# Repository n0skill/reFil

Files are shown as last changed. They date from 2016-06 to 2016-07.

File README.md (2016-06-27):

# reFil
A machine that makes filament suitable for 3D printers out of normally unrecycled plastic parts such as HDPE from bottle caps, failed prints etc.

# Folders
* schematics - All of the schematics made with KiCAD. Including the gerber files, kicad files (schematic, netlist, pcb, etc.)
* src - The source code running on the arduino nano (arduino/C/AVR ASM)
* mechanics - mechanical parts

# Material
The following material is needed for the whole project.

## Mechanical parts
The machine is made of lathed aluminium and brass.
All the plans will be available in the "mechanical" folder. Including 3D models, plans and specs

## Electrical parts
The controller board consists of an arduino nano and a custom board. Using a 24V power supply, a LM7805 regulator is used to drop down the voltage to a usable 5V signal to drive the logic. Since the drop is quite significant and the LM7805 is a simple linear regulator, a decent amount of heat will be produced. This can compromise the functionality of the circuit, so a heat sink has to be appended to it in order to better disipate the heat.

The board will be used to: 
1) display the current temperature
2) drive the motor
3) drive the heating element

### Temperature sensor
The temperature sensor consists of a PT1000 RTD as part of a voltage divider circuit. The conversion from voltage to temperature can be made by either: looking up a table, or using a formula.

Once the temperature is known, the arduino uses BCD encoding to controll the CD4543BE 7 segment display driver, which displays the temperature.

### Motor driver
The motor is a E192.24.246 Micromotors brushed DC thing. It has a 1:246 gearbox that allows it to move things with a high torque (at the expense of a lower rate of rotation. But we don't care about that)

It is using the 24V from the barrel jack and is toggled using a SRD-05VDC-SL-C relay from SONGLE industries.

### Heating element

The heating element is a simple nichrome wire that is also toggled with a relay on the 24V power line.

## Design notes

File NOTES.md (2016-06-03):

# Todo

## Currently
* Add temperature display
* Develop board to sense heat, control nichrome wire alimentation§ 

## Future Releases
* Add multiple thermal sensors to homogenize temp in core
* Add multiple thermal resistances to homogenize temp

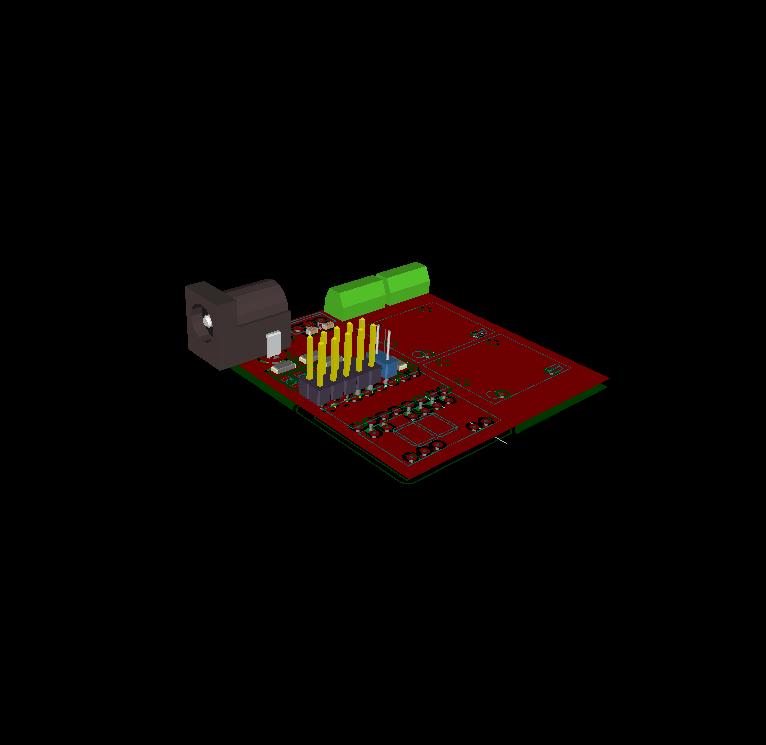
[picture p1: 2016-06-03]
schematics/reFil.jpg

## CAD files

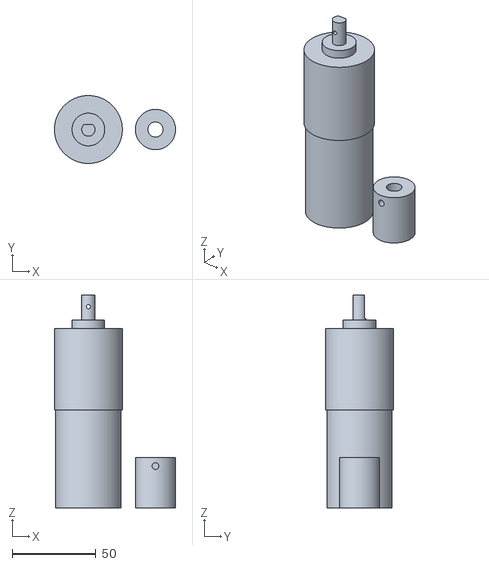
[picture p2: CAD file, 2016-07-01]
mechanic/parts.stl
72.2 x 40.5 x 127.0

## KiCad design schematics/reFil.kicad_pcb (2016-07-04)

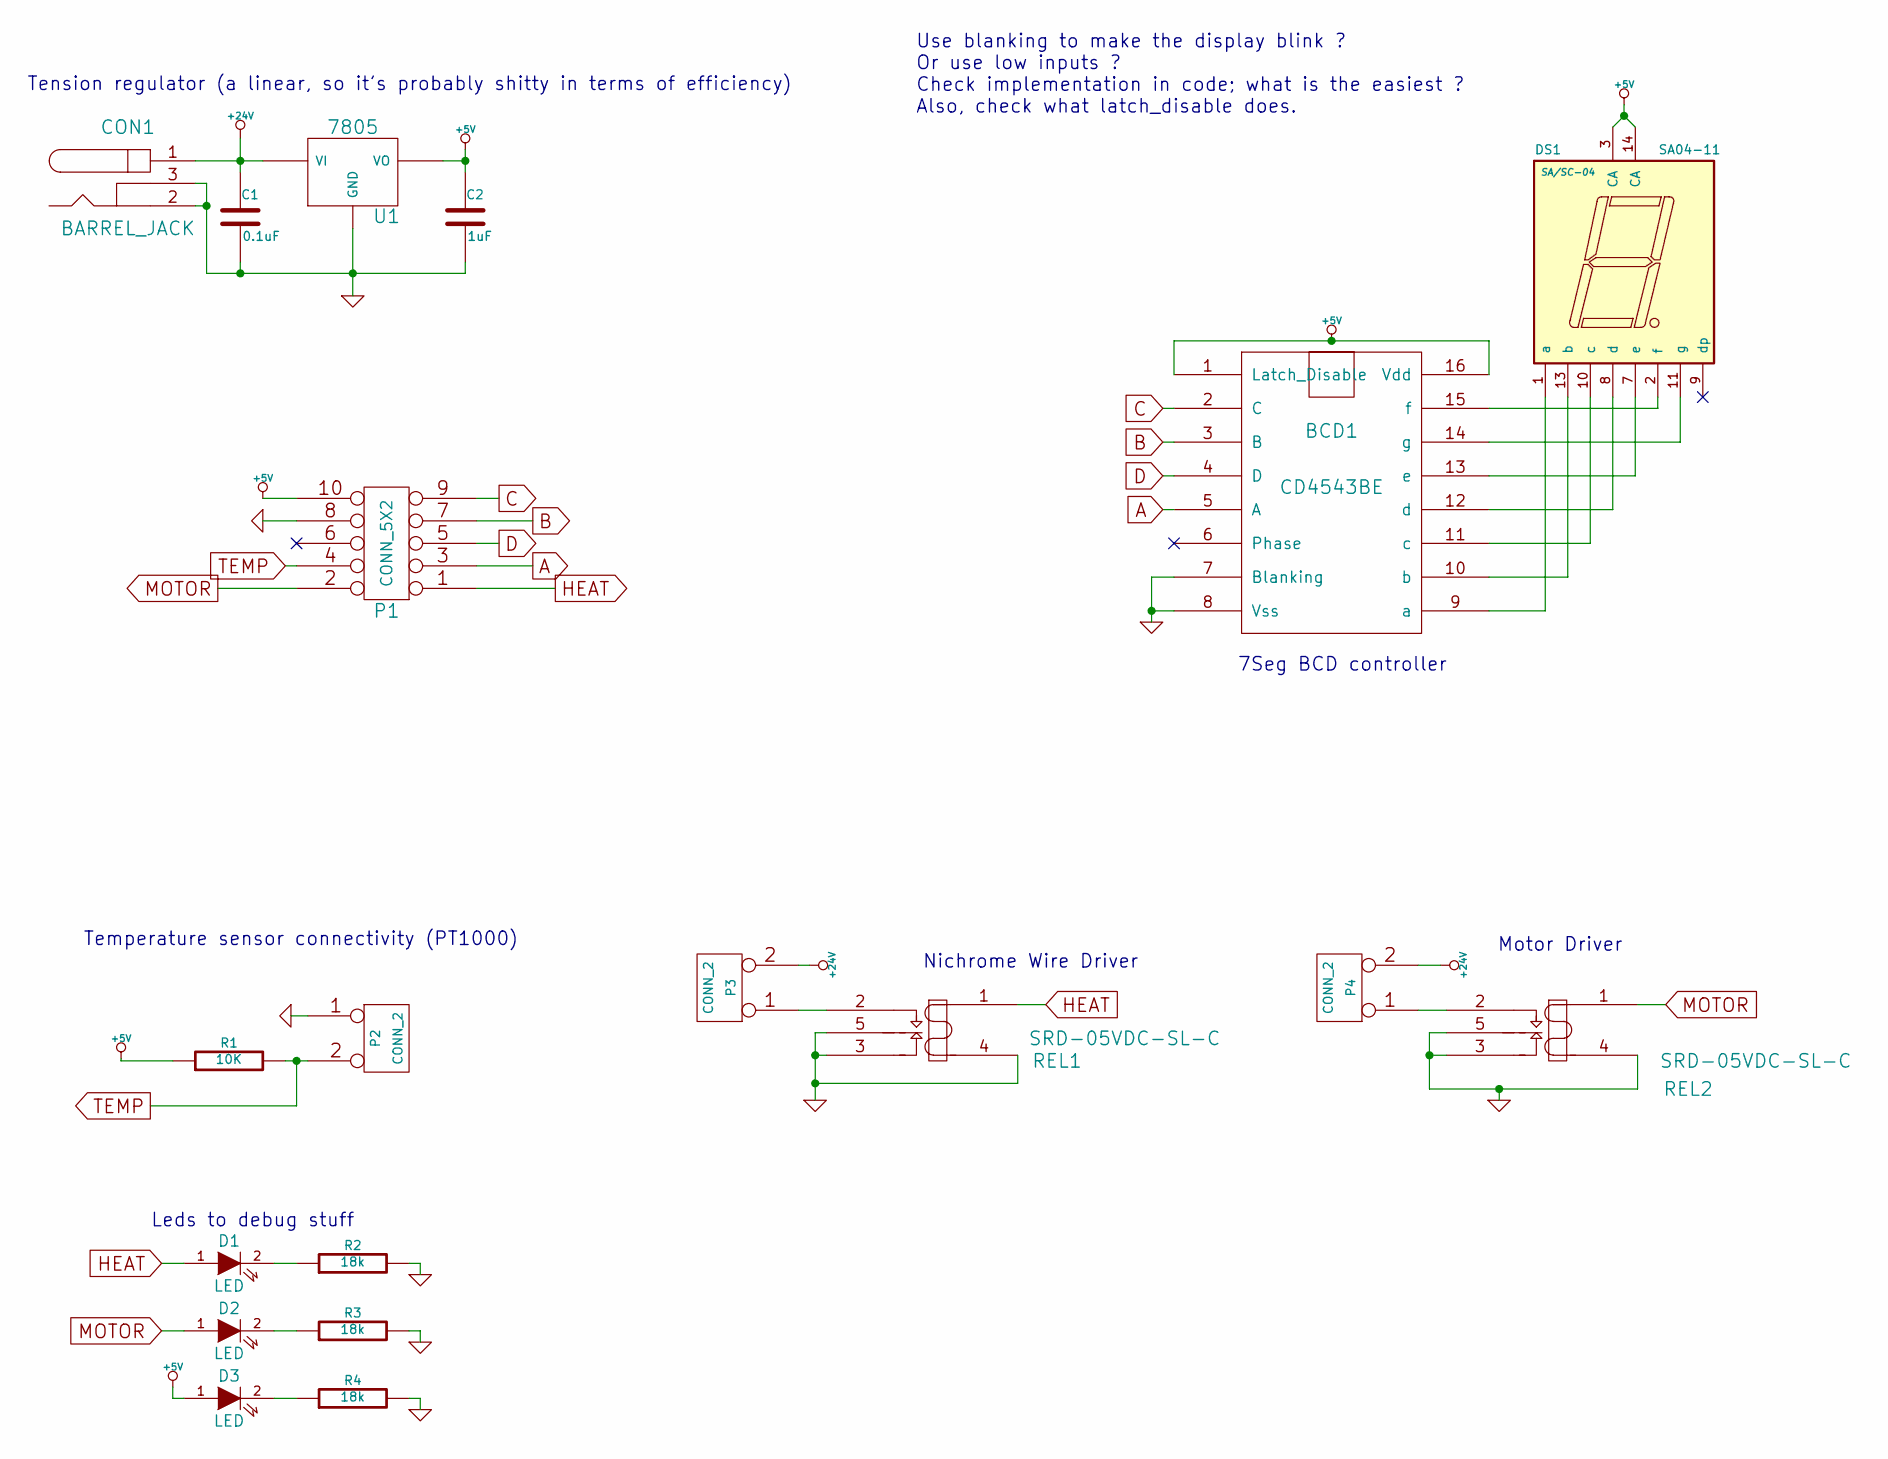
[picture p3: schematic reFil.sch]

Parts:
BCD1: CD4543BE
C1: 0.1uF
C2: 1uF
CON1: BARREL_JACK
D1, D2, D3: LED
DS1: SA04-11; SA/SC-04
P1: CONN_5X2
P2, P3, P4: CONN_2
R1: 10K
R2, R3, R4: 18k
REL1, REL2: SRD-05VDC-SL-C
U1: 7805

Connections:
+5V: BCD1.1 (Latch_Disable), BCD1.16 (Vdd), C2.1, D3.1 (A), DS1.3 (CA), DS1.14 (CA), P1.10, R1.1, U1.VO
+24V: C1.1, CON1.1, P3.2 (PM), P4.2 (PM), U1.VI
A: BCD1.5 (A), P1.3
B: BCD1.3 (B), P1.7
C: BCD1.2 (C), P1.9
D: BCD1.4 (D), P1.5
GND: BCD1.7 (Blanking), BCD1.8 (Vss), C1.2, C2.2, CON1.2, CON1.3, P1.8, P2.1, R2.2, R3.2, R4.2, REL1.3, REL1.4, REL1.5, REL2.3, REL2.4, REL2.5, U1.GND
HEAT: D1.1 (A), P1.1, REL1.1
MOTOR: D2.1 (A), P1.2, REL2.1
unnamed: D1.2 (K), R2.1
unnamed: P4.1, REL2.2
unnamed: P3.1, REL1.2
unnamed: BCD1.14 (g), DS1.11 (g)
unnamed: BCD1.15 (f), DS1.2 (f)
unnamed: BCD1.13 (e), DS1.7 (e)
unnamed: BCD1.12 (d), DS1.8 (d)
unnamed: BCD1.11 (c), DS1.10 (c)
unnamed: BCD1.10 (b), DS1.13 (b)
unnamed: BCD1.9 (a), DS1.1 (a)
unnamed: D2.2 (K), R3.1
unnamed: D3.2 (K), R4.1
TEMP: P1.4, P2.2 (PM), R1.2

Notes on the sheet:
7Seg BCD controller
Nichrome Wire Driver
Temperature sensor connectivity (PT1000)
Motor Driver
Use blanking to make the display blink ? Or use low inputs ? Check implementation in code; what is the easiest ? Also, check what latch_disable does.
Leds to debug stuff
Tension regulator (a linear, so it's probably shitty in terms of efficiency)

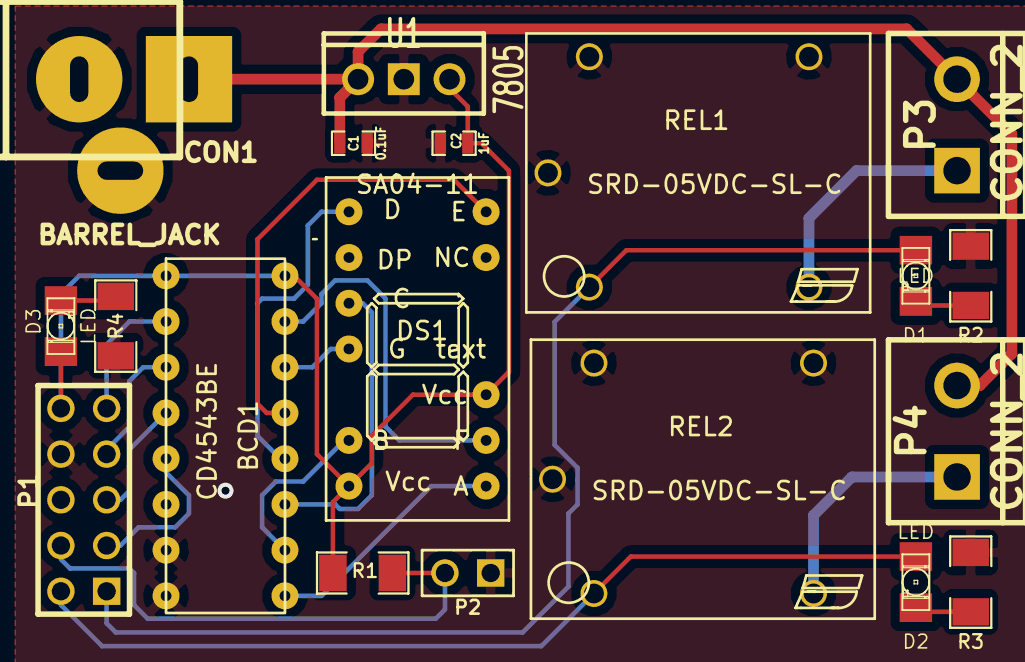
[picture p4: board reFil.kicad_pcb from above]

Board: 2 copper layers, 19 parts (0 on the bottom side), 22 nets.

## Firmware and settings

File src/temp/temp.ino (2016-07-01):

bool decaFlag       = LOW;
const int maxTemp   = 25;
const int margin    = 3;
const int targTemp  = 220;

void dispMode() {
  dispNum(targTemp, 200);
}

void heatingControl()
{
  float temp = getTemperature(getResistor());
  
  if(temp < maxTemp - margin) {
    digitalWrite(6, HIGH);
  }
  else if(temp > maxTemp + margin) {
    digitalWrite(6, LOW);
  }
}

float getResistor() {
  float Vout = (4.2 / 1024.0) * analogRead(A0); // Reads value on analog port 0
  delay(2);
  float dummyLoad = 10000.0; // ohms
  return (Vout * dummyLoad / (4.2 - Vout));
}

float getTemperature(float mesuredOhms) {
  float factA   = 3.9083e-3;
  float factB   = -5.775e-7;
  float nominal = 1000.0;

  float fltTemperature =  (-nominal * factA +
                          (sqrt(pow((nominal * factA), 2)
                          - 4 * nominal * factB * (nominal - mesuredOhms)))) /
                          float((2 * nominal * factB));
  Serial.print("Ohms: ");
  Serial.println(mesuredOhms);
  Serial.print("Temp: ");
  Serial.println(fltTemperature);
  Serial.print('\n');
  return fltTemperature;
}

void dispNull()
{
  digitalWrite(2, HIGH);
  digitalWrite(3, HIGH);
  digitalWrite(4, HIGH);
  digitalWrite(5, HIGH);
}
void dispNum(int num, int del)
{
  if(num >= 100)
  {
      disp((num/100)%10);
      delay(del);
      dispNull();
      delay(del/2);
  }
  if(num >= 10)
  {
      disp((num/10)%10);
      delay(del);
      dispNull();
      delay(del/2);
  }
  if(num >= 1) {
      disp(num%10);
      delay(del);
      dispNull();
      delay(del);
  }
    delay(del);
}

void disp(int number)
{
  byte BCD[11][4] =
  {
    {0, 0, 0, 0},
    {0, 0, 0, 1},
    {0, 0, 1, 0},
    {0, 0, 1, 1},
    {0, 1, 0, 0},
    {0, 1, 0, 1},
    {0, 1, 1, 0},
    {0, 1, 1, 1},
    {1, 0, 0, 0},
    {1, 0, 0, 1},
    {1, 0, 1, 0}
  };

  digitalWrite(2, BCD[number][3]);
  digitalWrite(3, BCD[number][2]);
  digitalWrite(4, BCD[number][1]);
  digitalWrite(5, BCD[number][0]);
}

bool readState()
{
  bool s = digitalRead(9);  return s;
}

void setup() {
  // put your setup code here, to run once:
  pinMode(2, OUTPUT);
  pinMode(3, OUTPUT);
  pinMode(4, OUTPUT);
  pinMode(5, OUTPUT);
  pinMode(6, OUTPUT);
  pinMode(7, OUTPUT);
  pinMode(9, INPUT);
  Serial.begin(9600);

  dispNull();
}

void loop() {
  if(readState())
  {
    digitalWrite(13, HIGH);
    dispMode();
    delay(200);
  }
  else 
  {
    digitalWrite(13, LOW);
    unsigned long currentMillis = millis();
    int temp = getTemperature(getResistor());
    dispNum(temp, 400);
    heatingControl();
  }
  delay(300);
}

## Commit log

2016-06-03 Fixing issues. Adding 3d view of the board
    [reFil-B_Cu.gbl, reFil-B_SilkS.gbo, reFil-F_Cu.gtl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]
2016-06-08 Better layout
    [reFil.kicad_pcb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]
2016-06-08 Add exported and gerber files
    [reFil-B_Cu.gbl, reFil-B_Mask.gbs, reFil-B_SilkS.gbo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]
2016-06-09 Electrolytic caps -> ceramic SMD caps. Also debugging LEDS.
2016-06-27 Fix relay footprint pins diameter. Rearrange layout of board for easier mounting.
    [reFil.kicad_pcb]
2016-06-27 Added sample arduino code
2016-07-01 Starting new layout. Better bornier placement.
    [reFil.kicad_pcb]
2016-07-01 Arduino code rework.
2016-07-01 Add corrected temp.ino file
    [temp.ino]
2016-07-01 Add 3D modeling of the motor and the shaft connector
    [parts.stl]
2016-07-04 New board layout and gerber export
    The 24V connectors (P3, P4) face the opposite side of the barrel jack.
    The power LED is now between the barrel jack and the P1 connector
    The thermistance connector is now below the temperature display
    [reFil.kicad_pcb]
2016-07-04 Fix gerber export
    Add the schematics/export folder to the repo
    [reFil-B_Cu.gbl, reFil-B_Mask.gbs, reFil-B_SilkS.gbo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]
